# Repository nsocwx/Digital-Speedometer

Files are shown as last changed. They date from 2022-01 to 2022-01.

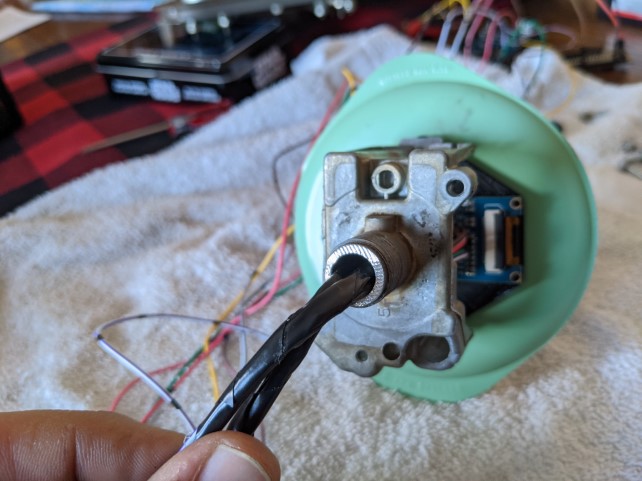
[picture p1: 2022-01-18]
Images/PXL_20220115_203457670.jpg

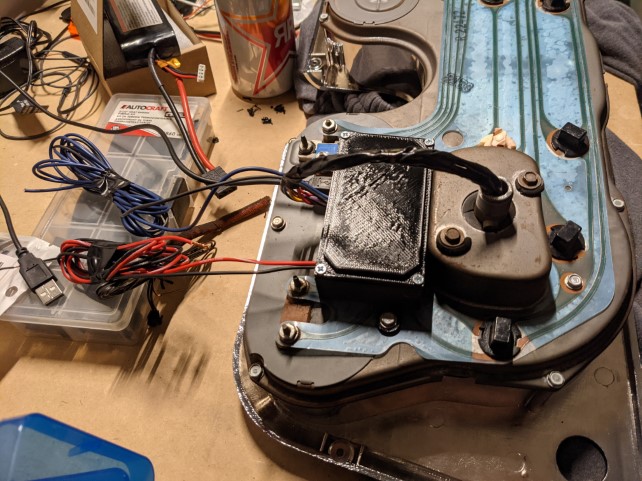
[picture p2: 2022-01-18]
Images/PXL_20220116_073353694.jpg

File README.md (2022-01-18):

# Digital-Speedometer
Arduino code for the digital speedometer project

I saw a speedometer mod for the 67-72 trucks made popular by ls1nova71 and brad_man_72 on this forum. They were swapping in digital a speedometer from a newer S10 and doing some graphics work to make the range right. I decided that I’m bad at printing graphics and making the hardware side work so I wanted to just make the existing gauge function without a spinning cable. My first attempt was to try using a speed controlled electric motor to ‘spin’ the speedometer input shaft at the right RPM to pretend to be the transmission. That test ended mostly in tears when I couldn’t get the electric motor to produce a consistent speed and it was also extremely noisy. I was ready to give up and get some Dakota digital cluster, but I was dead-set on getting this to work for $40 instead of $1400. Plus I wanted it to look as original as possible.

The idea was born to do something similar to the S10 speedo, but be able to control the exact position of the needle. I did some digging around online and found some guys creating aviation simulators using the X27 stepper motors to drive analog gauges using an Arduino. I also found some code samples of people reading vehicle speed via PWM VSS output with. I picked up a small digital screen to act as the odometer display vs trying again to make a motor spin the physical odometer. I already own a 3D printer so I used that to quickly make some of the components for holding everything, it could be done another way if you didn’t have one. EEPROM on the Arduino chip is used to store the odometer reading and pull it up each time without having to consume constant power.
I have a video of it working https://youtu.be/emJhqhSkUgA and some pictures of the process. I’ll need to follow up on this post with more information as I get the idea fully functional, I still need to get it in the truck and do a road test. Ideally I’d like to make this easy enough for someone to get the parts, put them together, and just make it work without having to get into coding or 3D modeling.

Here’s the material list I ended up with. I ended up shelling out $67, but that left me with extra parts for later projects.
Elegoo Arduino Nano
eBoot Buck voltage converter
Uctronics .96” OLED I2C
Cciyu? X27.168 stepper motor
Delphi 4way connector

I started out taking apart the c10 speedometer to see how much room I would have, I also learned a trick right off the bat to use a dinner fork for removing the dial. These factory gauges are like clockwork inside so you want to be as gentle on them as you can if you’re going to reuse anything. I went ahead and carefully removed the dial, face, odometer, all the gears, and the needle armature. The magnet at the rear spun by the cable was not as easy to remove and I decided to cut the outside end off and then pressed out the brass bushing that was inside. With all that out of the way I made a 3D print that would replace the part holding the gauge face and in doing so would also hold my screen and stepper motor. If you use the same components I did (OLED and Stepper) they should fit right in the model I designed. You’ll need to de-solder the pins from the OLED and replace them with wires right off the board due to clearance. The speedometer needle didn’t quite fit back on the X27 stepper shaft so I did print a new part of that too, alternatively you could drill it out with a 1mm drill bit.
With that all assembled I ran the wiring through the speedometer cable hole to the back of the cluster so it could connect up with the controller. I’ll provide a picture of the wiring diagram and a link here https://crcit.net/c/905a34e381de435d8df352c393757068. I then printed a box to hold the Arduino and buck board while sealing up the wiring with a lid. The connections were soldered to the pins of the Arduino, I’m not very good at soldering that kind of stuff, but it works just fine for now. I did also throw on a Deplhi weather pack connector so that the cluster is easier to remove later. The IO to the vehicle are ground, +12v, sensor ground, and VSS. In my case I’ll be connecting to the IGN circuit for power and then VSS output on my Holley Terminator X. I’ll run my sensor ground to where the engine harness is grounded just to be sure I’m getting the least possible resistance.

For the Arduino coding I went used the x25 stepper library from Guy Carpenter, SSD1306Ascii library from Bill Greiman, and a blog post from Mathew MCMillan about reading the VSS. Later on I switch to using the multiMap function from Rob Tillaart to handle the non-linear printout of the speedometer face.

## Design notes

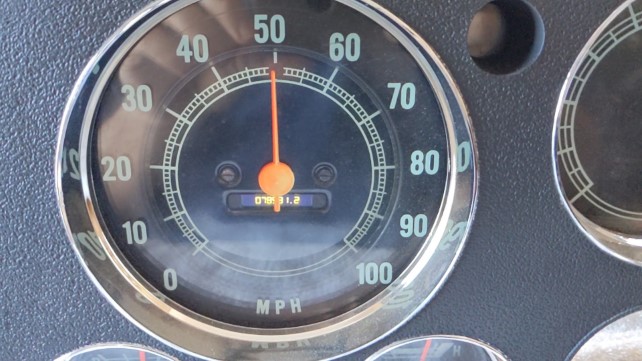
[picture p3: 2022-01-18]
Images/PXL_20220115_205712009_exported_201.jpg

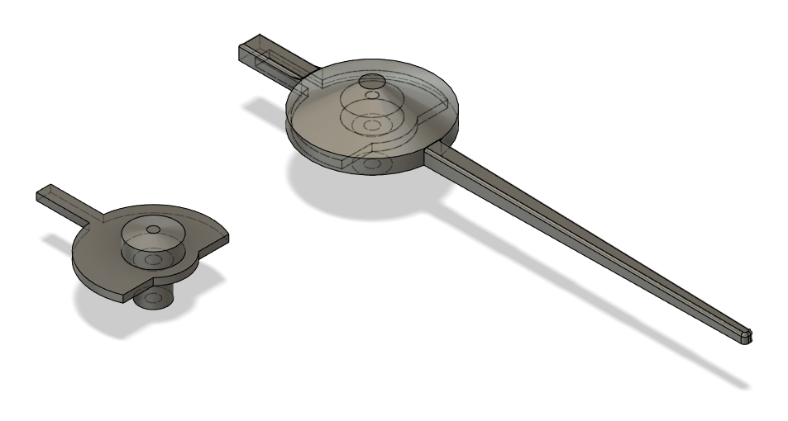
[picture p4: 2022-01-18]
Images/Dial and Peg.png

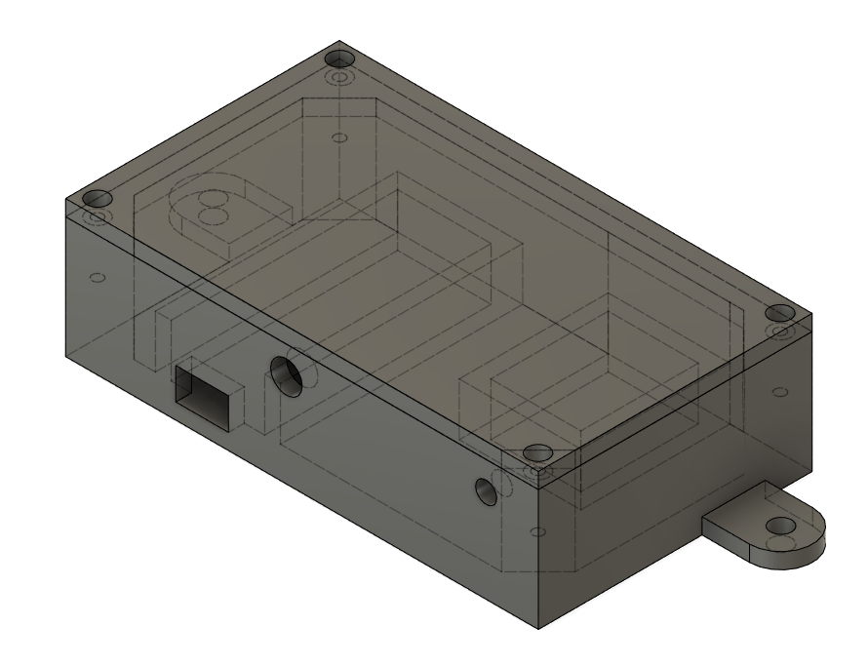
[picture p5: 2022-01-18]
Images/Enclosure.png

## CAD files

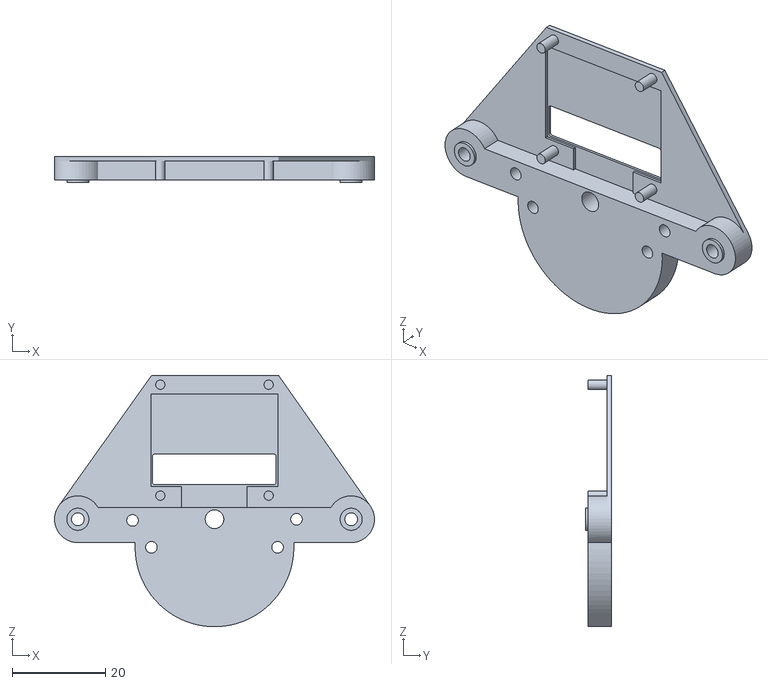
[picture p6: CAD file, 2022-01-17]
STL Files/Speedometer Mount V5.stl
68.5 x 5.55 x 53.8

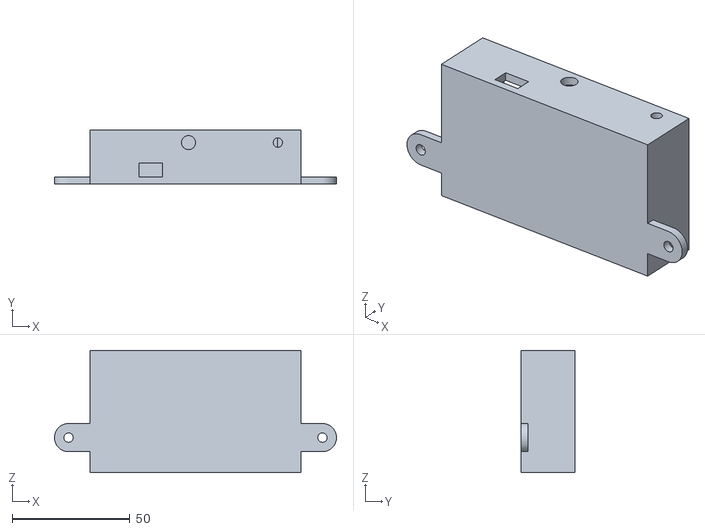
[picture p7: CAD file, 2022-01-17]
STL Files/ArduinoBox.stl
119.8 x 23.0 x 52.0

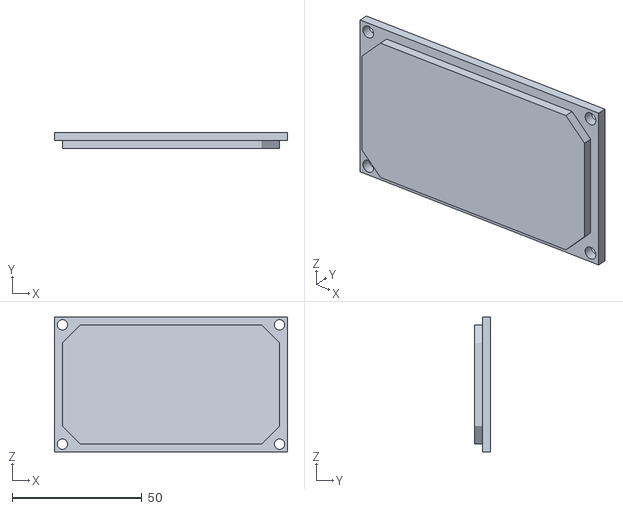
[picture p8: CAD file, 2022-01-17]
STL Files/ArduinoLid.stl
89.8 x 6.00 x 52.0

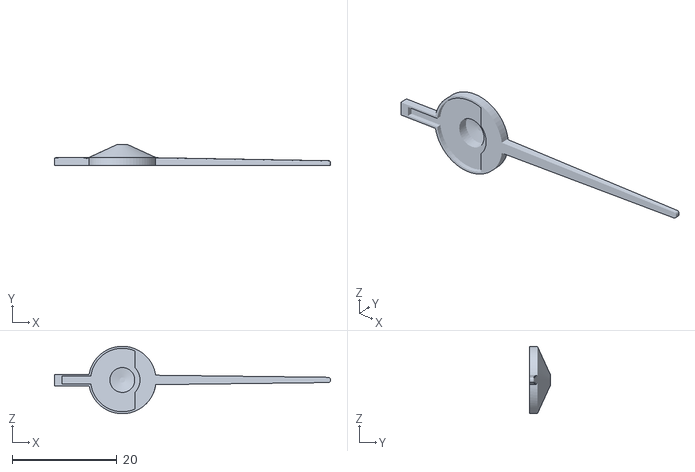
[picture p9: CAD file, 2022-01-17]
STL Files/DialNeedle.stl
52.6 x 4.00 x 12.9

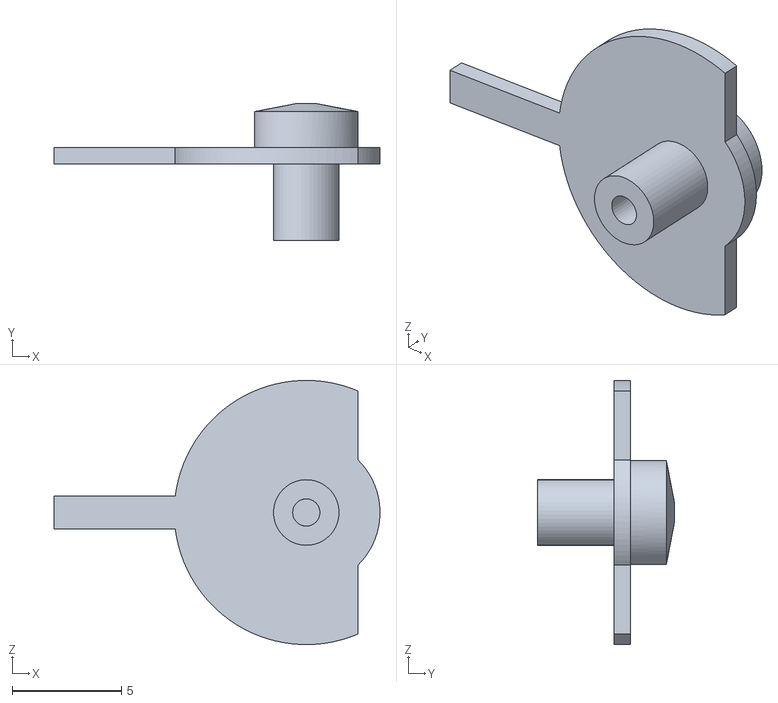
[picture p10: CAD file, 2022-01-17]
STL Files/DialPeg.stl
14.9 x 6.25 x 12.1

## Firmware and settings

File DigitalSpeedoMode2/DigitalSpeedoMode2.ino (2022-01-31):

// nsocwx 2022
// @nsocwx
// Digital speedometer
// VSS on car connects to pin 3
// see wiring diagram here https://crcit.net/c/905a34e381de435d8df352c393757068

// Speedometer stepper control for X27
// Odometer display for SSD1306 OLED
// Mileage has a memory limit of 1,073,741 given 4000ppm due to limitations of the 
// 'long' datatype before rolling over, less with higher ppm signals

/*****************************/
//includes
#include <SPI.h>
#include <Wire.h>
#include <SSD1306Ascii.h>
#include <SSD1306AsciiAvrI2c.h>
#include <SwitecX25.h>
#include <util/atomic.h>
#include <EEPROM.h>
//multiMap is now embedded as a function 
/*****************************/
//definitions
//A4 and A5 used for OLED screen
//screen
#define I2C_ADDRESS 0x3C
SSD1306AsciiAvrI2c display;
//dial
#define STEPS 945 // 315 degrees of range = 315x3 steps = 945 steps
SwitecX25 speedo(STEPS, 4, 5, 6, 7); //create object for speedometer with pins
//vss
#define VSSPin 3 //define pin to listen for VSS signal on
/*****************************/
//declarations
bool debug = false;//true for debug, false for production
unsigned int position; //set position for stepper motor
unsigned long mileage;//miles the vehicle has driven
unsigned int vss,VSS; //variable to store vehicle speed, times 100
unsigned long copy;//holds a copy of delta
volatile unsigned long delta; //holds the delta time, volatile so that it stored in RAM
unsigned long timeNew; //variable to store current check time
unsigned long timeOld;  //variable to store previous check time
const unsigned int pulsesPerMile = 4000;//variable to store vss ppm
const unsigned int pad = 10;//neeed to ensure convertMph contains a whole number instead of a fraction, may need 100 for 16k ppm signals
const unsigned int convertMph = (pad * 3600)/pulsesPerMile;
const unsigned long lowHz = 2000000000/pulsesPerMile;
const unsigned long highHz = 32000000/pulsesPerMile;
unsigned long mileageWhole; //mileage output to screen before decimal
unsigned int mileageTenth; //mileage output to screen after decimal
int out[] = {0,75,155,245,325,408,486,568,658,740,810}; //stepper positions for each 10mph
int in[] = {0,1000,2000,3000,4000,5000,6000,7000,8000,9000,10000}; //each 10mph x 100
/*****************************/
void setup() {
  if(debug){
    Serial.begin(115200);
  }
  //display
  EEPROM.get(0, mileage);  
  display.begin(&Adafruit128x64, I2C_ADDRESS);
  display.setFont(lcdnums12x16);
  display.clear();
  //dial
  speedo.zero();
  //vss
  attachInterrupt(digitalPinToInterrupt(VSSPin),VSSCount,FALLING);//create interrupt on VSSPin to run VSSCount() on each pulse
  delay(2000);
  timeOld = micros();
}
/*****************************/
void loop() {
  ATOMIC_BLOCK(ATOMIC_RESTORESTATE)
  {
    copy = delta; //read the delta in an atomic block to prevent changes mid read (4 cycles to read a long)
  }
  if((micros() - timeOld) > lowHz)//time long enough it must be less than ~1.8mph
  {
    vss = 0; //round vss below lowHz to 0
  }
  else if(copy < highHz) //time so short it must be over ~112.5mph 
  {
    //impossible value over highHz, debounce
  }
  else
  {
    vss = 100000000 / copy * convertMph / pad; //covert time between pulses to readable speed
  }
  position = multiMap(vss, in, out, 11); //map stepper position
  speedo.setPosition(position); //set speedo to mapped position
  updateDisplay();
  if(vss <= 0)
  {
    EEPROM.put(0,mileage);//if the vehicle is stopped, update EEPROM mileage
  }
  speedo.update();//move stepper to target location
  delay(5);
  if(debug){
    Serial.print((float)vss/100,2);
    Serial.print(" ");
    Serial.println(position);
  }
}
/*****************************/
void VSSCount() //runs when VSSPin sees an interrupt signal
{
  timeNew = micros();
  delta = (timeNew-timeOld);
  timeOld = timeNew;
  mileage++;
}
/*****************************/
unsigned int multiMap(int value, int* _in, int* _out, uint8_t size) //replaced multimap.h library
{
  // take care the value is within range
  if (value <= _in[0]) return _out[0];
  if (value >= _in[size-1]) return _out[size-1];

  // search right interval
  uint8_t pos = 1;  // _in[0] already tested
  while(value > _in[pos]) pos++;

  // this will handle all exact "points" in the _in array
  if (value == _in[pos]) return _out[pos];

  // interpolate in the right segment for the rest
  uint16_t result = map(value,_in[pos-1],_in[pos],_out[pos-1],_out[pos]);
  return result;
}
/*****************************/
void updateDisplay() //runs when called
{
  display.setCursor(17,0);//centers text
  //code to breakdown numbers for before and after decimal
  mileageWhole = mileage/pulsesPerMile;
  mileageTenth = (mileage*10/pulsesPerMile)%10;
  //outputs leading zeros to screen
  if(mileageWhole < 10){
    display.print("00000");
  }
  else if(mileageWhole < 100){
    display.print("0000");
  }
  else if(mileageWhole < 1000){
    display.print("000");
  }
  else if(mileageWhole < 10000){
    display.print("00");
  }
  else if(mileageWhole < 100000){
    display.print("0");
  }
  display.print(mileageWhole);//before decimal
  display.print("."); 
  display.println(mileageTenth);//after decimal
}

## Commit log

2022-01-18 switched from map to multiMap to handle non-linear speedometer layout and slowed stepper
2022-01-31 replaced multiMap and added Mode2 file for calculating speed on time between pulses instead of pulse counts
    [DigitalSpeedoMode2.ino]
2022-01-31 replaced cached delta time in low speed comparison with calculated delta
    function will evaluate time since last ISR run vs time calculated within the ISR
    [DigitalSpeedoMode2.ino]
